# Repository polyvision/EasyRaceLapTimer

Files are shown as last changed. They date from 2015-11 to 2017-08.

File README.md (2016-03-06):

EasyRaceLapTimer

# EasyRaceLapTimer

EasyRaceLapTimer is a complete open source IR lap time tracker all-in-one solution for FPV racing quads.



What you get with EasyRaceLaptimer:

**Features:**

* host system for tracking the laps
* IR transponders (code & schematic files for building them) with a transmitting range of 2 to 4 meters
* 63 available transponder IDs when using the project transponders
* changing the ID via a push button on the transponder, no additional programming required (started with version 0.3.1 of the transponders)
* update transponders with new code (Arduino hardware needed)
* setup guide for building your Raspberry PI host station
* the host station is also a WiFi access point to change configs etc on the fly
* monitoring mode, you can watch the stats with your mobile phones
* add your own team logo to the monitoring mode
* detailed stats about pilots and races
* sound effects for various events in a race
* TCP/IP and serial connections support for receiving lap times and commands from other time tracking systems
* export race events to PDF
* standard practice/ time trial mode
* competition mode for racing events with time penalties (satellites needed)
* automatic restarting of a race session after a specified idle time
* and much more comming soon

**Important notices**

EasyRaceLapTimer works basicly with any IR transponder, as long as you provide code for interpreting the IR pulses. Just have a look at the *ir_daemon* tool.

Be sure to use the full size of your SD card on the Raspberry PI

    sudo raspi-config

# Important information

The documentation for the project can be found in the [/docs](https://github.com/polyvision/EasyRaceLapTimer/tree/master/docs) directory.
There's also a huge [RCGroups](http://www.rcgroups.com/forums/showthread.php?t=2538917) thread with lots of answered questions, images etc.

# Version 0.5.x

You can download a SD card image for the PI of EasyRaceLapTimer on the following pages:

http://www.airbirds.de
http://www.easyracelaptimer.com

There's also an introduction video to the system.

# file structure

**/docs**
  documentation of nearly every part of the package

**/web**

the rails application

**/Arduino**

all arduino sketches

**/ir_daemon**

the cpp daemon for receiving the IR pulses

**/datasheets**

schematic files and more for transponders etc.

# Installation

fetch the source via git with the following command

    git clone git@github.com:polyvision/EasyRaceLapTimer.git

more details of each indivial package can be found in the *docs* folder

# Contributors
 * [Peter Provost](https://github.com/PProvost)
 * [Peisel](https://github.com/peisel)
 * [p3root](https://github.com/p3root)
 * [Sven Michel](https://github.com/svenmichel)

# license

The complete project uses the [GPL V3 license](http://www.gnu.org/licenses/gpl-3.0.de.html)

**development and sponsoring by [AirBirds](http://www.airbirds.de)**

Logo Title Text 1

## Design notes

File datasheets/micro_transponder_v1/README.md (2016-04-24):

This is a transponder intended for indoor microdrones. It's not that bright, 
which is fine when flying only a few feet from the receiver. It's also very 
small, which is good when every milligram counts.

It can still be programmed using alligator clips on the sides. The lettering 
on the back will show you which pad goes where (PB0, PB1, etc.). See the 
ATtiny85 datasheet for how they connect to the physical pins and their 
extended features.

Solder the +5V and GND pads to the power. If necessary, a +3.7V input (such as 
from a 1S lipo cell) should be enough.

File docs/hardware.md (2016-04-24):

EasyRaceLapTimer

# Hardware

## IR Transponder

    1x Infrared LED 950nm (Example: LD 274-3 or TSUS5202)
    1x Resistor 33 Ohm
    1x Resistor 330 Ohm
    1x Transistor NPN TO-92 45V 0,1A 0,5W (Example: 2N2222)
    1x ATTINY 85-20 PU, DIP-8
    1x IC socket for the ATTINY

You will need a solder pad for each transponder, on which you will solder everything on to.

**important notice**
Transponder version 0.2 & 0.3.1 are both compatible with ERLT. You can use both at the same time with ERLT. The only difference between 0.2 & 0.3.1 is the way you change the ID of the transonder.

## Transponder 0.3.1
Have a look at the [transponder datasheet](/datasheets/easy_race_lap_timer_transponder_attiny85_rev3_schematic.png) to see how all these parts are getting soldered.

## Transponder 0.2
Have a look at the [transponder datasheet](/datasheets/easy_race_lap_timer_transponder_attiny85_schematic.png) to see how all these parts are getting soldered.

## Programmer

You will need a programmer for the ATTINY85 if you want to upload the software on your own. Either use an Arduino as an ISP to accomplish this or get [this programmer](https://www.sparkfun.com/products/11801).

If you choose the Arduino ISP solution, here's an example [how to accomplish this](http://highlowtech.org/?p=1695).

## Host Station

    3x TSOP 31238 38kHz
    1x Raspberry Pi 2 (Raspberry Pi 1 is not officially supported)
    long wires to connect the TSOP IR sensors to the Raspberry GPIO ports
    1x USB WiFi stick (Example: Edimax EW-7811Un)
    5V micro USB power supply for the Raspberry Pi, eg: a powerbank

    optional, a buzzer: CPM 121, but any other buzzer which can stand 5V will make it too.

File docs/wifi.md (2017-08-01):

EasyRaceLapTimer

## WIFI AccessPoint

    SSID: EasyRaceLapTimer
    Password: 0123456789

## Host-IP

Use the following URL to connect with your mobile phone or whatever device you are using

     http://192.168.42.1

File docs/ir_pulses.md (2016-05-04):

EasyRaceLapTimer

# EasyRaceLapTimer - IR Pulses

9 bits are getting used for sending the transponder id (token). There's one thing to know in our approach. IR space pulses are also bits!
With 9 bits, we have 6 data bits, so 63 transponder IDs in total.

## the format

the length of a ZERO and ONE pulse can be found for example in

    Arduino/TransmitterAttiny85v0.2

*remember that each second pulse is actual a space for the ir receiver*

    1 PULSE | 2 PULSE | 3 PULSE | 4 PULSE | 5 PULSE | 6 PULSE | 7 PULSE | 8 PULSE | 9 PULSE

**1 PULSE | 2 PULSE**

  both must be set zero, it's our header

**3 PULSE | 4 PULSE | 5 PULSE | 6 PULSE | 7 PULSE | 8 PULSE**

  the actual data bits for representing our integer val or better said the id of the transponder

**9 PULSE**

  checksum bit. Set it to 1 if the number of ONES in the data bits is uneven

## example

    id 14: ZERO | ZERO | ZERO | ZERO | ONE | ONE | ONE | ZERO | ZERO
    id  3: ZERO | ZERO | ZERO | ZERO| ZERO | ZERO | ONE | ONE | ONE

if you log the output of your IR receiver you would get something like this for the above examples

    id 14: PULSE 300 | SPACE 300 | PULSE 300 | SPACE 300 | PULSE 600 | SPACE 600 | PULSE 600 | SPACE 300 | PULSE 300
    id  3: PULSE 300 | SPACE 300 | PULSE 300 | SPACE 300 | PULSE 300 | SPACE 300 | PULSE 600 | SPACE 600 | PULSE 600

please keep in mind that the pulse length differs a lot when using IR receivers, so they won't be 100% accurate

## some statistics

The longest time an ID (63) needs to be transmitted is 2x 250&#181;s + 7 * 650&#181;s = 5050&#181;s = 5.05ms

Assuming your quad top speed is 120km/h, that's 33.33 m/s  =  3.33 cm/ms. So the distance needed to transmit the ID is 15cm.

Distance needed with a speed of 90km/h = 25 m/s = 2,5 cm/ms -> 13.75 cm distance

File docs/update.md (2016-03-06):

EasyRaceLapTimer

Instructions for updating to the next stable version. After updating the system, you need to restart the Raspberry PI.

# updating to 0.5
    cd ~/EasyRaceLapTimer
    git pull origin master

    cd ~/EasyRaceLapTimer/web
    bundle
    RAILS_ENV=production rake db:migrate
    RAILS_ENV=production rake assets:precompile
    
# updating from v0.3 to v0.4

    sudo apt-get install redis-server
    cd ~/EasyRaceLapTimer
    git pull origin master

    cd ~/EasyRaceLapTimer/ir_daemon
    qmake ir_daemon.pro
    make
    sudo ./ir_daemon --use_standard_gpio_sensor_pins (call this cmd after the update, this sets the standard pin layout for the sensors etc)

    cd ~/EasyRaceLapTimer/web
    bundle
    RAILS_ENV=production rake db:migrate
    RAILS_ENV=production rake assets:precompile

# updating to v0.3

    cd ~/EasyRaceLapTimer
    git pull origin master

    cd ~/EasyRaceLapTimer/ir_daemon
    sudo apt-get install libudev-dev
    qmake ir_daemon.pro
    make

    cd ~/EasyRaceLapTimer/web
    bundle
    RAILS_ENV=production rake db:migrate
    RAILS_ENV=production rake assets:precompile

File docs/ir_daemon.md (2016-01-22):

EasyRaceLapTimer

# EasyRaceLapTimer IR_DAEMON

The ir_daemon is a C++ daemon running in the background of your Raspberry PI. It's responsible for decoding IR data, receiving and sending commands from and to various sources etc.

## requirements

    sudo apt-get install  qt5-default libcurl4-openssl-dev libudev-dev

## compilation

    cd ir_daemon
    qmake ir_daemon.pro
    make
    sudo ./ir_daemon --use_standard_gpio_sensor_pins
    sudo ./ir_daemon [for starting]

## command line options

show some debug output

    --debug

listing available serial ports

    --list_serial_ports

set serial port

        --set_com_port_index INDEX

set buzzer pin

        --set_buzzer_pin PIN

use standard pin layout

        --use_standard_gpio_sensor_pins

use pin layout for displayotron 3k HATs

        --use_dot3k_hat_pin_setup

enable satellite mode

        --enable_satellite_mode

disable satellite mode

        --disable_satellite_mode

set web host URL, used for the satellite to set the right IP of the main station

        --set_web_host http://<IP>/

        default:

        --set_web_host http://localhost/

## data sources

   The ir_daemon can read data from TCP/IP sockets, serial connections and of course from the GPIO interface of the Raspberry PI.

## TCP Connection

The ir_daemon is listening on port 3006 for incomming connections. All commands need
a \n behind the #.

## commands

The following commands are available for serial and TCP/IP connections

*starting a new race*

    START_NEW_RACE#

*resetting*    

    RESET#

*tracking a new lap time*

    LAP_TIME <TOKEN/ID> <MILLISECONDS>#

* getting the last scanned token by the ir_daemon *

    LAST_SCANNED_TOKEN#

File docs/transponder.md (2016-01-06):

EasyRaceLapTimer

# Transponder setup

# Requirements

You will need the Arduino software and an ISP programmer (Arduino Nano, UNO, [Tiny AVR programmer](https://www.sparkfun.com/products/11801) ...)

Now add this url to the additional boards  in your Arduino IDE in the settings menu:

    https://raw.githubusercontent.com/damellis/attiny/ide-1.6.x-boards-manager/package_damellis_attiny_index.json

# Step 1

  Set the settings of your Arduino software like in this screenshot

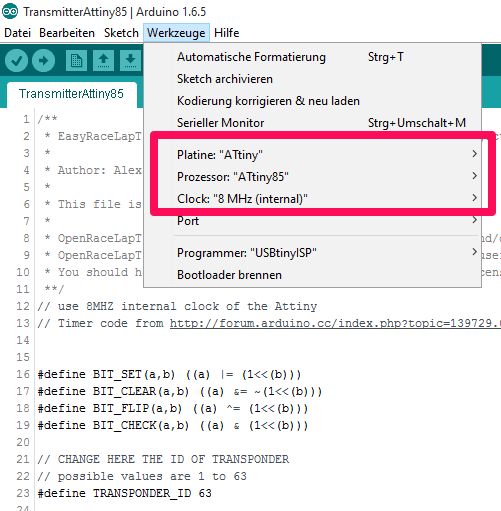
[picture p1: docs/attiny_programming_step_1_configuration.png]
  

# Step 2

  burn the bootloader

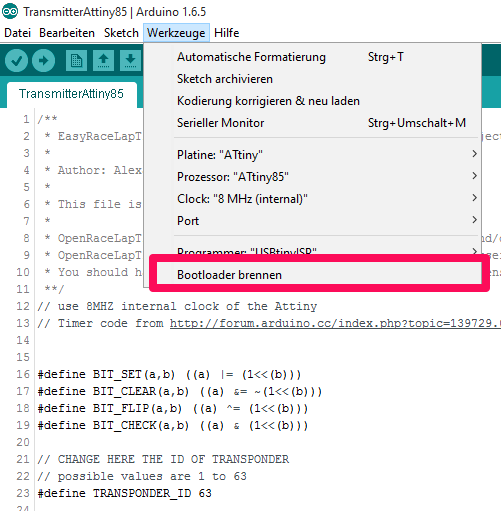
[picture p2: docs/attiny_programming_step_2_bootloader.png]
  

# Step 3

  change the ID of your transponder

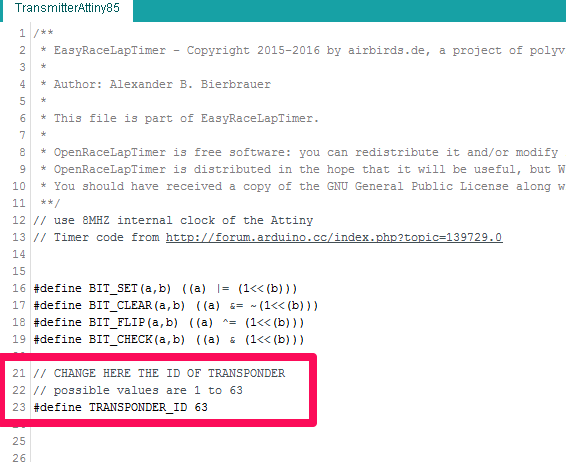
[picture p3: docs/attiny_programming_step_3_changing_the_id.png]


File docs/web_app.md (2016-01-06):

EasyRaceLapTimer

# EasyRaceLapTimer web application

this setup is based on Raspian JESSIE

## install requirements

switch to the **web** folder in your EasyRaceLapTimer folder

    sudo apt-get install ruby2.1-dev libssl-dev apache2 apache2-threaded-dev libapr1-dev redis-server libaprutil1-dev  imagemagick wkhtmltopdf redis-server
    sudo gem install bundler
    bundle config build.nokogiri --use-system-libraries
    sudo  gem install nokogiri -v "1.6.6.2"
    bundle
    sudo gem install passenger
    sudo passenger-install-apache2-module
    RAILS_ENV=production rake db:create
    RAILS_ENV=production rake db:migrate
    RAILS_ENV=production rake db:seed
    RAILS_ENV=production rake assets:precompile

## Apache setup

copy this code

    LoadModule passenger_module /var/lib/gems/2.1.0/gems/passenger-5.0.21/buildout/apache2/mod_passenger.so
    <IfModule mod_passenger.c>
      PassengerRoot /var/lib/gems/2.1.0/gems/passenger-5.0.21
      PassengerDefaultRuby /usr/bin/ruby2.1
    </IfModule>

and add it to the apache2 config via

    sudo nano /etc/apache2/apache2.conf

place the code near the following lines in the file

    # Include module configuration:
    IncludeOptional mods-enabled/*.load
    IncludeOptional mods-enabled/*.conf

## Rails Webapp setup

    rake db:create
    rake db:migrate
    rake db:seed

default credentials are:

    user: admin@easyracelaptimer.com
    password: defaultpw

## Rails Webapp development
for running rails in dev mode, you need to run these two commands in seperate processes (e.g. terminal windows). The app uses sqlite for it's database

    rails s

starting with v0.4, REACT gets used for various parts

    cd web
    npm install  (installing node modules)
    webpack (compiles the JS to app/assets/javascripts/main.js)

## API

be sure to change **localhost:3000** to the correct ip of the host station

**tracking a lap**

    POST http://localhost:3000/api/v1/lap_track

or

    GET http://localhost:3000/api/v1/lap_track/create

**starting a new race**

    GET http://localhost:3000/api/v1/race_session/new

**getting data of the current race session**

    GET http://localhost:3000/api/v1/monitor

needed params
 * transponder_token
 * lap_time_in_ms

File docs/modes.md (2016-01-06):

EasyRaceLapTimer

# EasyRaceLapTimer modes in detail

## standard mode aka practice / time trial mode

The most used mode. Fly your laps, the system tracks your time. You can check later on who was the fastest in the practice / event etc.

## competition mode

The mode used for racing events. The system sums up the time for each lap of a pilot. The one with the fastest summary time is the winner. If used with satellites, you can define time penalties if a satellite doesn't get passed.

In competition mode, you must set manually the pilots who are attending the race. You can define new transponder tokens especially for this mode or simple keep the old ones.

If you enable the hot seat feature in the competition mode, you don't need to add pilots. If a pilot passes the sensor, he will get added automaticly to the current race.

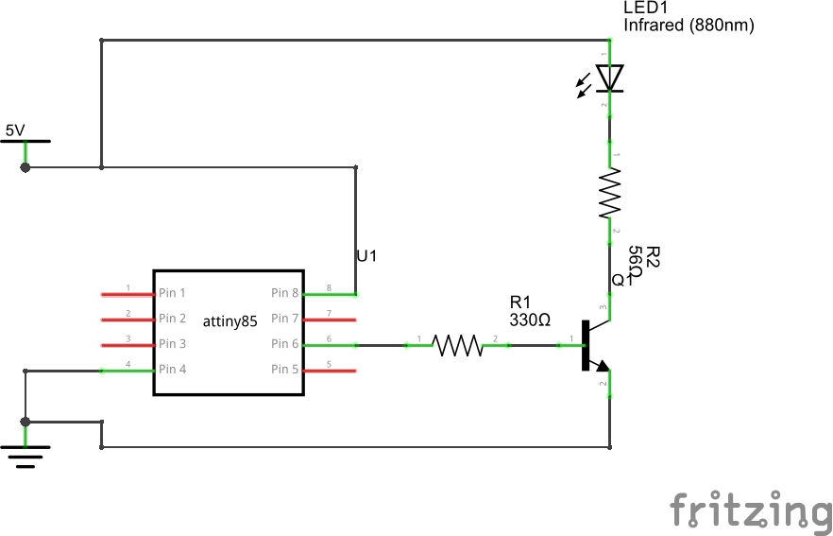
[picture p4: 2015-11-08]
datasheets/easy_race_lap_timer_transponder_attiny85_schematic.png

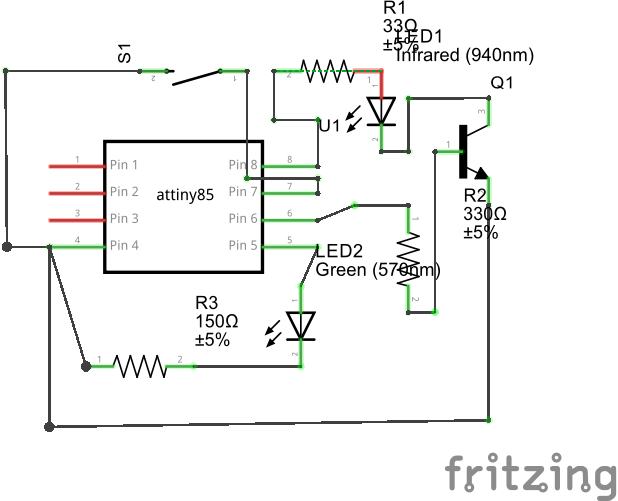
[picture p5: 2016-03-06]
datasheets/easy_race_lap_timer_transponder_attiny85_rev3_schematic.png

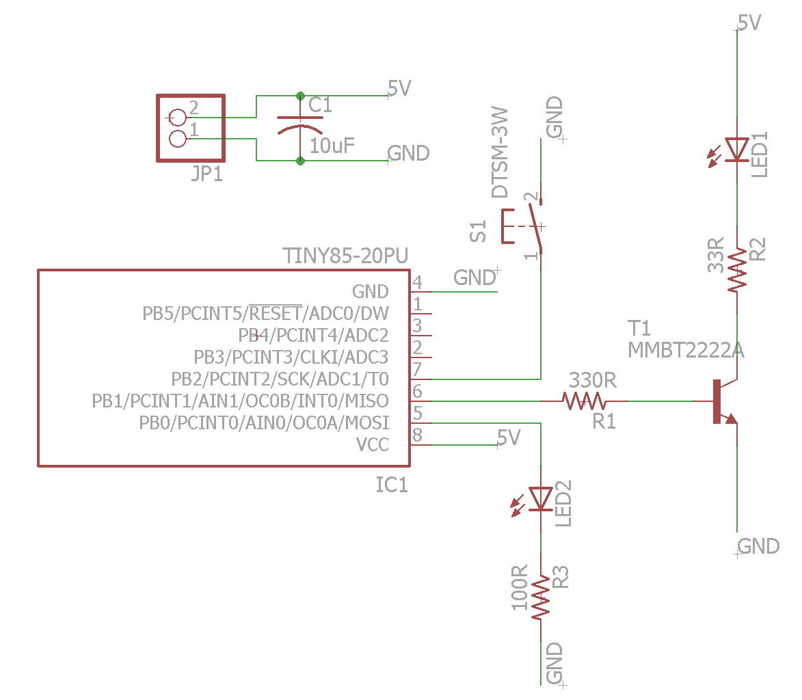
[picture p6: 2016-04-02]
datasheets/SMD Transponder/SMD R1.4 Schematic.PNG

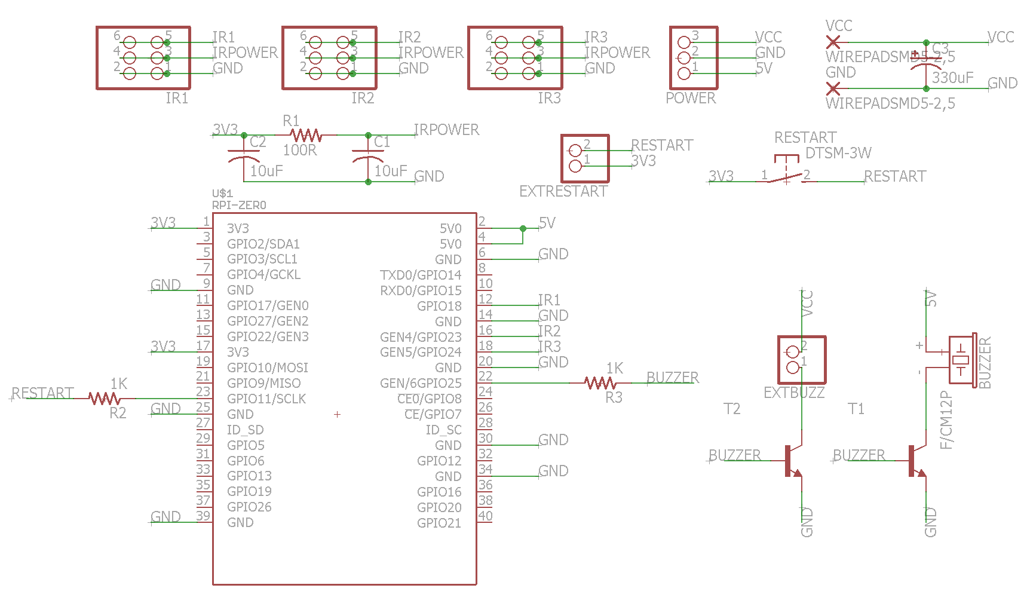
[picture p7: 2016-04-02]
datasheets/Raspberry Pi Hat Base Station/BaseStation R1.1 Schematic.png

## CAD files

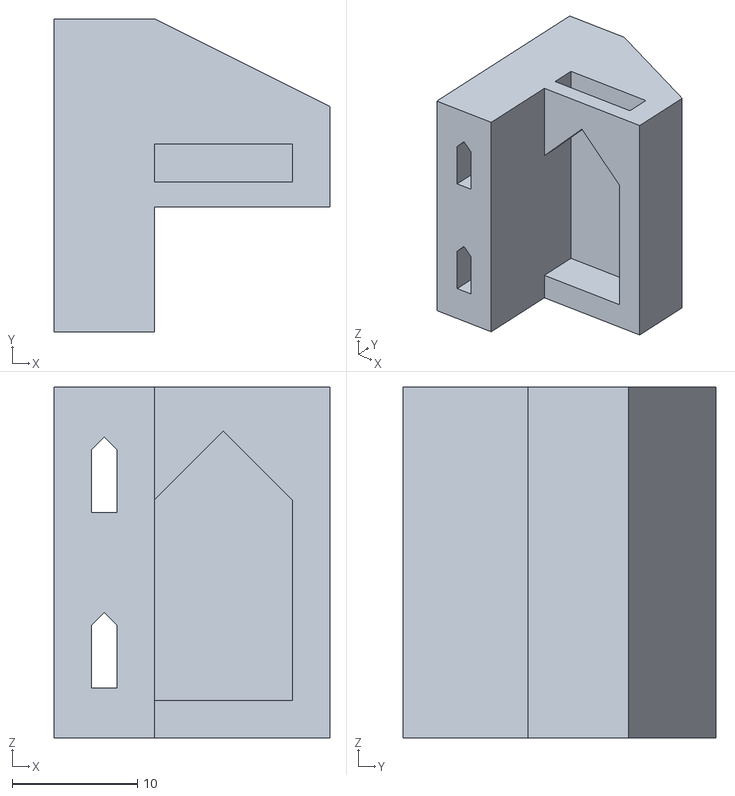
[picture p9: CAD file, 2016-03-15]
3d_print_files/ERLT Sensor Right - TSOP31238.stl
22.0 x 25.0 x 28.0

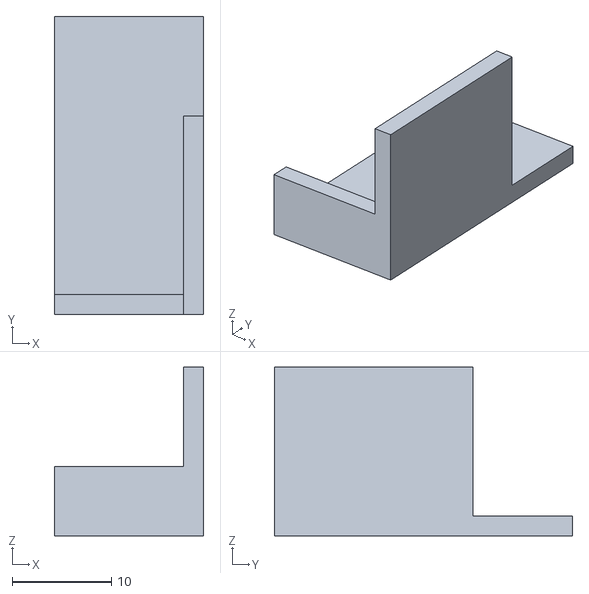
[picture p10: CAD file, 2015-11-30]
3d_print_files/sensor_case_left.stl
15.0 x 30.0 x 17.0

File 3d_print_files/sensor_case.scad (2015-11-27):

cube([15,30,2]);
translate([0,0,2]){
    cube([15,2,5]);
}

translate([13,0,2]){
    cube([2,20,15]);
}

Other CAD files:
3d_print_files/ERLT Sensor Left - TSOP31238.stl
3d_print_files/sensor_case.stl
3d_print_files/ERLT Sensor Left - TSOP31238.skp
3d_print_files/ERLT Sensor Right - TSOP31238.skp

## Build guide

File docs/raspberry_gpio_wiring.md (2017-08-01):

EasyRaceLapTimer

# EasyRaceLapTimer Raspberry2 PI GPIO wiring

The wiring should be the same of Raspberry 1 hardware. If not, feel free to update the docs.

# wiring
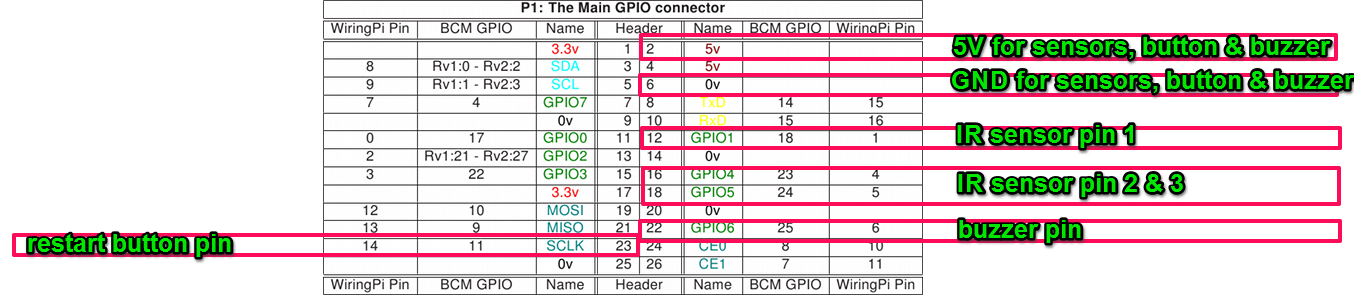
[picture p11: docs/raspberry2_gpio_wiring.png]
"GPIO wiring"


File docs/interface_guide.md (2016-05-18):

EasyRaceLapTimer

# Website pages and functions

This guide will walk you through the pages and functions of the EasyRaceLapTimer website interface.

When you go to the web interface (usually through http://192.168.42.1), you'll see this screen:

main

## Login

You can login by clicking the Login button on top.
Default admin login info is:

Email: admin@easyracelaptimer.com 
Password: defaultpw

After you logged in as admin, you'll see this screen:

afterlogin

Let's walk through the different pages.

## Race Director

On the Race Director page, you have control over the race in progress. You can start/stop races, check the latest detected Transponder ID, fastest laps, number of laps per pilot, etc.

## Configuration

### System

The System page allows you to:

* start Standard Race Tracking
* start a Competition Race (more advanced options)
* go to Pilots and Sound Configuration
* set some configuration values
* upload your own logo 
* shutdown the Raspberry Pi

### Users

The Users page allows you to create, edit and remove user profiles. You can also assign roles to users (admin/race director).

users

### Pilots

On the Pilots page allows you to add, remove and edit pilots info. 

pilots

* To add a pilot, fill in his/her Name, Transponder Token, Quad name and press Create.
* To remove a pilot, click the Delete button behind the pilots info in the list.
* To edit a pilots info, click the Edit button behind the pilots info in the list.
* You can remove the Transponder Token from the pilot by clicking the Remove Token button.

There is also the option to add an avatar to each pilot. This can be done by clicking the Edit button after adding the pilot to the list.

### Soundeffects

On the Pilots page allows you to adjust the audio Volume by pressing the buttons. You can also test the audio by pressing the Play Test Sound button.

soundeffects

You can also upload your own Race Event Soundeffects by clicking the Upload Wav button after every audio event listed.

## Monitor

The Monitor page allows everyone (pilots/audience) to follow the timing. It shows fastest laptime, last laptime, number of laps, average laptime per pilot.

## History

On the History page, you have an overview of all sessions. Each session shows some brief info like the name, mode, number of pilots, number of laps, fastest lap, fastest pilot and the average laptime of the session.

Behind each session row, you have the option to delete the session from history or export the results as a PDF-document.

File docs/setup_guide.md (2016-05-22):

EasyRaceLapTimer

# Complete Setup Guide

This guide will walk you through manually setting up the software on your Raspberry Pi. You will
need to have your Pi connected to the internet to perform these steps.

As an alternative, you can use the provided Raspbian disk image file if you have the exact same
hardware as described in the hardware setup doc and just want to get started right away. But if you want
to know how to build the software up from scratch, this guide is for you!

## Preparing your Raspberry Pi

Before you begin, you should download and install a Raspian Jessie image onto an 8GB (or more) micro SD card.
For more information about setting up your Pi, see https://www.raspberrypi.org/help/quick-start-guide/.

The next thing is to ensure that you are using all of your SD card. Execute the following command:

    sudo raspi-config

and choose "Expand Filesystem".

If you used NOOBS to install Raspbian, you can probably skip this step, but if you're unsure, try it anyway
and it will tell you if there is nothing to do.

While you are in raspi-config, you might also want to change whether the Pi boots to a desktop (GUI) or to
the command line. Since the system runs "headless", not running the full GUI can free up resources. If you're
unsure, leave it set to the default.

## Get the Code

On the Pi, execute the following commands to pull the source from this GitHub repository:

    cd ~
    git clone https://github.com/polyvision/EasyRaceLapTimer.git

## Build the IR Daemon

The IR Daemon listens for the signals coming from the IR detectors and sends them to the Rails app via
a web API.

To build it, perform the following steps:

    cd ~/EasyRaceLapTimer/ir_daemon
    sudo apt-get install  qt5-default libcurl4-openssl-dev libudev-dev wiringpi
    qmake ir_daemon.pro
    make
    sudo ./ir_daemon --use_standard_gpio_sensor_pins

## Build the Rails App

This is the main system app, and it provides the web UI & API.

To build it, perform the following steps (note: some of these steps will take a while to run, so be patient):

    cd ~/EasyRaceLapTimer/web/
    sudo apt-get update
    sudo apt-get install ruby2.1-dev libssl-dev apache2 apache2-threaded-dev libapr1-dev redis-server libaprutil1-dev imagemagick libsqlite3-dev bridge-utils wkhtmltopdf hostapd dnsmasq
    sudo gem install bundler
    bundle config build.nokogiri --use-system-libraries
    sudo  gem install nokogiri -v "1.6.6.2"
    bundle
    RAILS_ENV=production rake db:create db:migrate db:seed assets:precompile
    sudo gem install passenger
    sudo passenger-install-apache2-module

## Configure Apache Webserver

First you need to setup the new site in Apache:

    cd ~/EasyRaceLapTimer
    sudo cp config_files/000-default.conf /etc/apache2/sites-available/000-default.conf

Then, open /etc/apache2/apache2.conf using this command:

    sudo nano /etc/apache2/apache2.conf

In that file, find the following lines:

    # Include module configuration:
    IncludeOptional mods-enabled/*.load
    IncludeOptional mods-enabled/*.conf

and paste the following just before them

    LoadModule passenger_module /var/lib/gems/2.1.0/gems/passenger-5.0.21/buildout/apache2/mod_passenger.so
    <IfModule mod_passenger.c>
      PassengerRoot /var/lib/gems/2.1.0/gems/passenger-5.0.21
      PassengerDefaultRuby /usr/bin/ruby2.1
    </IfModule>

## Configure Linux Networking

The easiest way to setup the network is to use the provided interfaces file:

    sudo cp config_files/network_interfaces /etc/network/interfaces

But if you know linux networking, you might want to just compare the existing file with
the provided one and setup the network accordingly.

## Configure the Wireless Hotspot

If you are using the recommended EDIMAX WiFi adapter, you should skip to the section "Configuring
the EDIMAX WiFi Adapter".

If you are using another WiFi interface with your Pi, you should look at the following articles
to learn how to configure your interface for AP mode.

* http://jacobsalmela.com/raspberry-pi-and-routing-turning-a-pi-into-a-router/
* http://elinux.org/RPI-Wireless-Hotspot

You will then want to adapt the instructions below for your adapter.

### Configuring the EDIMAX WiFi Adapter

Source: http://www.daveconroy.com/turn-your-raspberry-pi-into-a-wifi-hotspot-with-edimax-nano-usb-ew-7811un-rtl8188cus-chipset/

First you need to get the updated driver for the RTL8188CUS chipset used in this interface:

    cd ~
    wget http://www.daveconroy.com/wp3/wp-content/uploads/2013/07/hostapd.zip
    unzip hostapd.zip
    sudo mv /usr/sbin/hostapd /usr/sbin/hostapd.bak
    sudo mv hostapd /usr/sbin/hostapd.edimax
    sudo ln -sf /usr/sbin/hostapd.edimax /usr/sbin/hostapd
    sudo chown root.root /usr/sbin/hostapd
    sudo chmod 755 /usr/sbin/hostapd
    cd ~/EasyRaceLapTimer
    sudo cp config_files/hostapd.conf /etc/hostapd/

Then reboot your Pi:

    sudo reboot

After rebooting, you can test your configuration using the following command:

    sudo hostapd -dd /etc/hostapd/hostapd.conf

If it runs as expected, add it to your system startup:

    sudo nano /etc/default/hostapd

Then uncomment and update the following line:

    DAEMON_CONF="/etc/hostapd/hostapd.conf"

Next you will configure the DNS & DHCP settings:

    sudo nano /etc/dnsmasq.conf

Find the line that begins with "#interface" and edit it as follows:

    interface=wlan0

In the same file, find the line that begins with "#dhcp-range" and edit it as follows:

    dhcp-range=192.168.42.2,192.168.42.100,255.255.255.0,12h    

Save and close the file.

## Check Permissions for wkhtmltopdf
Double check that the wkhtmltopdf is executable.  This ensures that "PDF Export" will work for race history.

    sudo chmod +x /home/pi/EasyRaceLapTimer/web/bin/wkhtmltopdf

## Check Permissions for sidekiq.sh
Double check that the sidekiq.sh script is executable

    sudo chmod +x /home/pi/EasyRaceLapTimer/web/start_sidekiq.sh

## Configure the IR Daemon and Sidekiq (sound events) to launch at startup

Edit the following file:

    sudo nano /etc/rc.local

Then add the following to the bottom of the file, just before "exit":

    (sleep 1; /home/pi/EasyRaceLapTimer/ir_daemon/ir_daemon > /var/log/ir_daemon.log 2>&1 &) || /bin/true
    (sleep 1; /home/pi/EasyRaceLapTimer/web/start_sidekiq.sh > /var/log/sidekiq.log 2>&1 &) || /bin/true

## Troubleshooting sound effects playback

Sidekiq is responsible for playback of audio for sound effects.  Depending on the version and source fo Ruby installed, Sidekiq may not launch at startup.  If this is the case, please try these steps.

Locate the path to the Sidekiq binary that is being used by Ruby:

    which sidekiq

Edit the following file:

    sudo nano ~/EasyRaceLapTimer/web/start_sidekiq.sh

Edit the following line by replacing sidekiq with the /full/path/to/sidekiq:

    RAILS_ENV=production sidekiq -c 1

## To login to the website:

Connect to your raspberry Pi (via Ethernet or the Pi's Wifi Access Point).

Default password for the Wifi AP is "raspberry".

Open the webpage, if you're connected via Wifi AP the address is http://192.168.42.1

Default credentials are:

    user: admin@easyracelaptimer.com
    password: defaultpw

*You are done!*

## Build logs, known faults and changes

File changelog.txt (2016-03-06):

version 0.5.1

* added autorestart of race sessions via idle time
* added transmitter code 0.3.1
* bug fixing

version 0.4b2

* webview monitor updates itself all 2 seconds
* sending monitor UDP broadcast after tracking a lack via port 3333
* renamed config values for better understanding
* improved GUI (not finished yet)
* added hot seat feature for competition mode

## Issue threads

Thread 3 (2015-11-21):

How to update the files in Raspberry PI

peisel, 2015-11-21:
It would be nice to have a description/manual how to simple update the solution on the Raspberry Pi to latest version.

PProvost, 2015-11-24:
I agree. For my most recent update, after pulling the new source, I had to reset the database using the rake commands in the setup guide. It is probably a good idea to explain that to people.

polyvision, 2015-11-29:
wrote update docs for 0.3 ;)

Closed 2015-11-29.

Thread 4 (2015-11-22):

Upload Soundfiles doesn't work

peisel, 2015-11-22:
Test with short .wav files, .mp3 files. Upload Button don't work.

polyvision, 2015-11-25:
fixed in upcomming v0.3

workaround for current version: go to sound page, reload the page, upload works. curious bug ;)

PProvost, 2015-12-17:
I'm in 0.4b2 and unable to upload sound files using the webpage. Nothing helpful in the apache2 error log file, and nothing at all in the easyracelaptimer.error.log file.

Closed 2015-11-25.

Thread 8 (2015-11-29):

Shutdown Button - No Function

peisel, 2015-11-29:
I did update via Update - not image. Shutdown Button didn't work after Popup OK. PI didn't shudown.

polyvision, 2015-11-29:
did u recompile the ir_daemon and made a restart of the complete system? the shutdown button should work

peisel, 2015-11-29:
Forget to restart the complete system - works

Closed 2015-11-29.

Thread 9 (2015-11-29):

Race Restart Button didn't work?!

peisel, 2015-11-29:
Update via commands - not the complete image.

I use a buzzer button - contact closed as long i pressed the button. Connected to 23(signal),25(gnd) pin. Did i miss something?
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

peisel, 2015-11-29:
Sorry i see it in my own picture ... wire wrong ... ;-)

peisel, 2015-11-29:
Sorry wiring is ok - issue exist

polyvision, 2015-11-29:
same here, try again after the restart ;)

peisel, 2015-11-29:
hmm ... how should it work ... i thought the current race will reset? or how should this button work?

polyvision, 2015-11-30:
if u push the button, a new race will get started

peisel, 2015-12-02:
Ich bekomme es nicht zum laufen ... der schalter verbindet pin 23 und gnd solange wie ich ihn gedrückt halte. Ich hatte einmal einen Eintrag "Race November 29, 2015 22:40	0	0	0.0s		0.0s" dies konnte ich aber nicht reproduzieren, Ich benutze img 0.2 mit dem manuellen update auf 0.3. Den Pin habe ich auch einmal mit Kabel auf gnd überbrückt aber dort das gleiche liegt also nicht am schalter.... ratlos

polyvision, 2015-12-03:
Ich habe jetzt gerade nicht das Layout vor mir. Aber Du hast + an den PIN-Eingang gelegt? Hm, aber warte bis ich nachher nachschauen kann, bevor ich jetzt Mist rede ;)

peisel, 2015-12-03:
Der Taster verbindet das Signal von PIN 23 (Rotes Kabel) mit GND Pin 25 (schwarzes Kabel) wenn er gedrückt wird, ich gehe davon aus etwas spinnt mit software oder pi nicht?

polyvision, 2015-12-04:
wie lange drückst du denn? also 1sek muss gedrückt werden damit etwas passiert, ist so in der software programmiert

peisel, 2015-12-05:
Keine Ahnung ... lange gedrückt, kurz gedrückt ... ich warte mal ab auf 0.4 ...

peisel, 2015-12-07:
when i connect pin 23 and 24 for a second it works ... is it right? Pin 23 reacts when its connected with a + signal?

Closed 2015-12-08.

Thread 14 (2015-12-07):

Setting an ID Without Reprogramming

frezik, 2015-12-07:
I noticed that the racer's unique ID has to be set in the code, with a maximum of 63 IDs.  It would be nice to be able to set this ID prior to a race without a full flash of the chip.

There are a few ways this could work. I2C, SPI, and Serial should all be available on the ATtiny85 chip. SPI in slave mode is a little wonky on Arduino (the library doesn't support slave mode directly). All three may have timing issues in the Arduino library due to the lack of a 16MHz crystal driving the chip.

A crude but effective means would be similar to how memory chips work. You set binary data with one bit per wire (across however many wires you have), and then "latch" a signal on another wire. When the chip sees the latch happen, it reads the values off the data wires to build the word.

With the IR LED taking up one wire, the ATtiny85 only gives us 3 data wires plus 1 latch. By doing this twice, you could send 6 bits, for 64 possible values.

A slightly easier way is to bump up to an ATtiny2313 and use a whole 8 wires. Comparing prices on Digi Key, this would add less than $1 to the cost for single orders, and an almost insignificant cost on bulk orders. The pin headers for this are also a tiny cost.

A further extension could be to use the Ardunio EEPROM library:

https://www.arduino.cc/en/Reference/EEPROM

Which would allow for maintaining the ID in between reboots.

polyvision, 2015-12-09:
There will be a new revision of the  transponders in the future. But at present, I'm focussing on the software.

polyvision, 2016-01-11:
Solved in a new rev of the transponders. Soon to be released.

Closed 2016-01-11.

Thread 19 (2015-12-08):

Update Documentation

peisel, 2015-12-08:
Please add commands for:
- clean up race history
- clean up racers
- Reset User Passwords
- edit "Admin" Account

polyvision, 2015-12-09:
What do you mean by "clean up racers" and "clean up race history"? One single button to delete them all?

peisel, 2015-12-09:
Not a ring to rule them all ... a button to delete all --- better would be a list functionality for delete ... like select all and unselect some ... to delete most of them ...

PProvost, 2015-12-17:
If you want to toss the entire database and start clean, you can do this:

    RAILS_ENV=production rake db:drop db:create db:migrate db:seed

The first command (drop) tosses the current database, then create, migrate and seed recreate it (similar to the steps in the setup guide).

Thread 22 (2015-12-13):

Monitor API - update speed

FieserKiller, 2015-12-13:
Hi,
I built an app which announces lap times, check it out: https://play.google.com/store/apps/details?id=de.my_fuzzy_logic.laptimeannouncer
Tested it on field today. We had 3 smartphones polling the interface every second. It worked, but I noticed a varying delay between a copter passing the sensor and his last_lap time changing in monitor.
It is usually ~5sec behind, sometimes a few seconds more or less.

polyvision, 2015-12-13:
Hi,

yes that's true at present. I'm firing and forget the "send lap time" requests at present, QT handles then the requests.
I'm planning to change this portion of the code, so that these requests will arrive faster in the rails app.

FieserKiller, 2015-12-13:
The perfect solution from the point of view of my app would be broadcasting monitor JSON over UDP to the network, whenever data changes.
This way we would cover 3 topics at the same time:
- Service discovery. Every device would find EasyLapTimers address easily by listening to UDP broadcasts on its WiFi interface
- No polling anymore, less load, less bandwith and power usage
- (Almost) real time monitoring data for everyone :)

polyvision, 2015-12-21:
It's implemented now, please test it ;)
Port is 33333.

There's now also a config value udp_broadcast_address which defaults to: 192.168.42.1

Maybe 127.0.0.1 is a better solution, dunno. First time, I'm doing something with UDP broadcasts.

polyvision, 2016-01-04:
The update speed in v0.4RC1 should be now even faster

FieserKiller, 2016-01-04:
Back from holidays - will test and implement into LaptimeAnnouncer App :) Thx

fape, 2016-11-06:
Do you know why udp broadcast was removed on 0.6 branch? see 222493ca67ae545545f2e10878e69f29285fb60d

Closed 2016-01-04.

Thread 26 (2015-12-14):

Auto update race panel

cmenard, 2015-12-14:
Currently one has to manually refresh the page to get updates during a race.  I'm wondering if we could use something like this https://github.com/chrismccord/sync to automatically update the page during a race session.

polyvision, 2015-12-15:
this gem looks interesting, will check it out

PProvost, 2015-12-17:
Honestly, I quick-n-dirty solution would be to use client-side auto refresh logic.

Something simple like:

    <meta http-equiv="refresh" content="10" />

Would do nicely.

polyvision, 2015-12-18:
fixed in upcomming v0.4b, made a quick solution. The gem also uses websockets. I would have the same problem like now with actioncable (also websockets).

Closed 2015-12-18.

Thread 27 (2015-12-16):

Building Transponder

sniperxnl, 2015-12-16:
I see no crystal on the Attiny85? Is that for a reason?

sniperxnl, 2015-12-16:
I have build the same on

1x Attiny85
1x 330Ohm
1x 56Ohm
1x NPN BC547
1x Vishay 950NM (i wait for the osram)

So i think i build a next one with crystal 8 MHZ and 2 x 10 pF on the gnd.

What do you think?

PProvost, 2015-12-17:
What do you think you need a crystal for? Are you thinking you need an external oscillator?

The transponder code expects the ATTiny to be running at 8MHz which the built-in oscillator is quite capable of handling. Trust me. I have a dozen of these working on my desk using nothing more than an ATTiny85, a 2n222A, two resistors and the IR LED.

polyvision, 2015-12-17:
Hey, there. You don't need a crystal. Like PProvost said, the internal oscillator works just fine in 8Mhz mode. Just burn the bootloader with 8Mhz (like described in the docs) and you're done.

Closed 2015-12-21.

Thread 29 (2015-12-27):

Add FPV Channel for Pilots

peisel, 2015-12-27:
Add in Configuration and Race Overview - Choose from 40 Ch

warrenjeffs, 2016-05-31:
please add this to the pilot page, will make it alot easier to know what channel they should be on.

mindmined, 2016-06-23:
sorry, has to fix my hardware and I am quite busy at the moment.
But I will add a nice setup menu, as soon as possible. But I bricked my arduino and have to solder a new one in.
Soon you see my new hardware with Lap Time in the OSD.

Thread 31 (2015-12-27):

Host/Slave System for Competition

peisel, 2015-12-27:
I would be nice to connect several pi/sensors stations together - so team pilots could have their own station and they could connect together for competition races. I think you did this allready?

pompushko, 2019-04-30:
Nice Feature  would be , if use start and finish slave stations. and couple of stations in the middle to see time between portals

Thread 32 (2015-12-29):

Updated docs to include steps to install and build dependency wiringPi

Nandox7, 2015-12-29:
The wiringPi library is missing from the installations steps.

polyvision, 2016-01-04:
Would be great if you update the docs!

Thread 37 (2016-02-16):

Feature Request: Multicolor LED output for gates based on last pilot through.

c3h5, 2016-02-16:
I typically fly in small groups all via FPV and basically we cannot keep track of each other.
So I had an idea to allow color assignment to pilot’s transponder IDs in the software and have a hardware output from the Raspberry Pi to set multi colored LED.
The purpose would be so that the Raspberry Pi could control the multicolored LED display attached to a gate so that the pilots flying could see who flew though a gate last.
Example my friends color is blue and I see the gate ahead is blue thus he beat me to it.
But then some laps later I see a gate ahead and it’s my color, thus I know I’ve lapped him.

Hope the above makes sense

I think this would be great in a multi gate setup
and also having the option of the gates auto clearing of color after a users predefined amount of time.

frezik, 2016-02-16:
I happen to have been working with RGB LEDs of late. An easy way to do this is with GPIO, which would give you the 3 primary RGB colors, plus the 3 secondaries by combining any two of the 3 primaries.

It's possible to get any arbitrary color using PWM on each of the RGB colors, but the Pi only has 1 PWM output. You can use an Arduino to take an i2c or serial signal that sets the color, and then use its own PWM outputs to the LEDs.

c3h5, 2016-02-17:
This would be fine as the number of people flying at the same time is typically small and we care more about a quick head to head battle than say a best time. And powering a Pi/LED display is no big deal when you have plenty of old 3s lipo nobody is using. :)

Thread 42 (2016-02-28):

Spoken Lap Times

kah00na, 2016-02-28:
When the Raspberry Pi 2 is connected to an external set of speakers, it would be good if each lap time was spoken out loud so racers would know if they were getting faster or slower.  Lap times can currently be reviewed in the pilot's history through the web GUI after the race is over, but you don't know how you are doing during the race itself unless you have someone watching the Monitor page and yelling out the times.

polyvision, 2016-05-02:
Problem at present is the text-to-speech caps of the PI. I've tested some packages but the output is really  bad.

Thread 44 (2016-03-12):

Reliability of IR Protocol Desgin for Partial Codes

frezik, 2016-03-12:
Looking over the existing IR protocol design:

https://github.com/polyvision/EasyRaceLapTimer/blob/master/docs/ir_pulses.md

I thought of a situation that doesn't seem to have a solution in the current system (though I may have missed something). The data stream starts with a 300us pulse and 300us space as a header. It then alternates between pulses and spaces, with a 1-bit sent as 600us and 0-bit as 300us.

Here's the issue: let's say the quadcopter flies in range of the sensor just as it sends the second bit after the header (which will be a space). The sensor will see this as a single long space after the last quadcopter left the sensor range. Let's say the next pulse and space (third and fourth bits after the header) both happen to be 0. This will be detected as the start of a new header, and bits will be parsed from there as if the code had just started--obviously not the correct situation!

Since the quadcopter's transponder will keep cycling the same code, the next header will be parsed as a pair of zeros in the middle of a code. The software doesn't have a chance to recover.

This can be corrected by dealing with a longer code. The current equation on the page suggests that in the worst-case of a quad travelling at 120km/s, the complete code would be transmitted over the course of 15cm of movement. I suggest designing for 3 or more sensors wired in parallel to allow a budget of at least 30cm. This would be a marginal additional cost with slightly more complicated wiring.

With that change, the header can be changed to a 1200us pulse/1200us space. This allows the sensor code to easily throw away the initial partial code, then pick up the next good code. Duplicates sent in a short time period need to be thrown out, but that's true, anyway.

I'd also recommend sensor designers wire multiple receivers for at least 60cm. That gives the system the best chance of correctly picking up the code.

c7devteam, 2016-03-13:
OK, I get the point. I made some thoughts about this in the past too.

The only solution I can up was, add a crystal (or use another IC) to the transponder for more correct pulses (timings) and do the parsing of the codes via interrupts in the ir_daemon.

Regarding your solution, don't know if this will fix the problem (neither do I know if my suggestion will fix it) but let's try yours.

polyvision, 2016-03-13:
OK, I get the point. I made some thoughts about this in the past too.

The only solution I can up was, add a crystal (or use another IC) to the transponder for more correct pulses (timings) and do the parsing of the codes via interrupts in the ir_daemon.

Regarding your solution, don't know if this will fix the problem (neither do I know if my suggestion will fix it) but let's try yours.

frezik, 2016-03-13:
I think it will be a combination of the two--longer header length, and an external crystal.

I've been playing with some transmitters on a custom PCB, and using LIRC to get the raw pulse/space data. With an attiny85 on its internal 8MHz clock, the data is all over the place.

I then pulled the attiny out of its socket and used jumpers from an Arduino (atmega328, 16MHz external crystal) to hit the right pins in the socket to drive the circuit. I used a sketch based on the sendRaw example from the Arduino-IRremote library, which you can see here:

http://pastebin.com/cM0NEcM4

Using the same circuit board, those numbers came out as clean as can be expected for IR pulses. I doubt the switch to the atmega matters.  It's the clock that's doing it.

As another experiment, I set the attiny85 for a 1 MHz internal clock. Those numbers came out almost as clean as the Arduino. The only problem was that it wasn't quite fast enough to switch at 300us. The data bits almost always came out at 600us.

The one thing is that from these tests, I would have expected this to be all but unusable. Seems like there's enough people using the system "in the wild" that somebody would have noticed that by now.

frezik, 2016-03-13:
After testing again, I think it's actually working fine with the 300us timing on the 1MHz clock. See:

https://github.com/frezik/EasyRaceLapTimer/blob/ir_daemon_v2/Arduino/TransmitterAttiny85v0.4/TransmitterAttiny85v0.4.ino

This also removes the delay at the end of the loop. I believe this is what may have been helping the previous system to recover. With a longer header length, it shouldn't be necessary. In practice, removing that delay is likely to shorten the effective distance needed for a clean read, since the transmitter can send more duplicate codes.

It also does an infinite loop with `while(1){...}`.  This is faster than waiting for `loop()` to be continuously called.

The docs were also cleaned up, with issue #43 cleaned up, and the protocol header redefined. The math at the end for the length of the transmission was also corrected for the new header. I figured it was worth keeping the previous doc around while transmitters are still out there, so I moved it into `ir_pulses_old.md`.

This branch also has some of my work for the v2 ir_daemon, which runs off LIRC.

ABLomas, 2016-09-15:
If you are changing protocol anyway (requires transponder reflashing, etc) - maybe add single-bit checksum too?
One bit checksum for 6 bits of data (for example, XOR'ed) - does not add much payload, but would filter random ID's appearing in list (this happens sometimes). Usually ID can be read several times when going trough gate, so ID with mistake is not big issue.

I'm not sure how this plays with new ir_daemon - maybe requires many changes?

slacker87, 2016-09-15:
Pass the id number through an xmodem crc and then tack the resulting checksum at the end of the signal. If on the rx side the checksum doesnt add up to the id sent, discard as its an invalid (1/2 received) signal. This should work regardless of timing.

shamshir1972, 2017-03-12:
frezik, how do i run ir daemon v2, i.ve already install lirc dan cpan

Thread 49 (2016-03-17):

UDP multicast of raw gate events

rccrashcraven, 2016-03-17:
Rather than clients polling for monitor data, and rather than getting all data, it might make sense to have a udp multicast of each raw event. This would cut down a lot is load on the Pi server. Rather than the full session plus data json structure, just send a simplied token, lap num, lap time structure.

frezik, 2016-03-17:
I like this idea in theory. However, multicast can be tricky to setup in practice. It may be particularly tricky on Android and iOS clients (not sure, really).

If load on the Pi due to polling is high, we may be better off finding a way to reduce or offload that.

rccrashcraven, 2016-03-17:
Ok. I haven't looked at ease of multicast listeners on any thing except windows.

How many tcp client sockets can the PI hold open?
Maybe clients request connection, are given a port, reconnect at that port, then they are send raw gate events.

I have to think the load on PI would be much lighter than the same clients banging away at xxx/api/v1/monitor and which sends about many times the data required on a per event quad/gate event.

NicoLoco, 2016-05-06:
I like the idea of the Pi multicasting the information.
I would be careful with UDP as there is no guarantee the packets will be received, and Wifi can be flaky, especially in an environment full of other 2.4GHz and 5.8GHz signals.

Maybe we could setup a system where the server multicasts the last 10 events periodically via UDP.
If a client realises he is missing some events (missing IDs), it can send a request to the server asking for all events starting from event number X. This request would be handled in TCP so we know the server will receive it, and the reply will be received too.

SSPW, 2016-05-06:
I agree UDP is fire and forgot with no guarantees.

I think the only thing that should be guaranteed in the ERLT system is the PI actually has all the data and one master connection (a laptop of other that is the race admin portal). Any other system hanging off the PI, like a text to speech client is secondary and should be prioritized that way.

I race with a group that has 30 guys turn out. Lets say 20 try to listen using a client that is polling the normal monitoring api. Its going to bog down the PI. Sure there should only be 5-6 connected. But they aren't going to start and stop their connections. Its a bad scheme.

Alternative is a TCP server that client registers with transponder ID or all data. Then client then only gets event data they registered for. Client is simple. Server is more complicated.

WIFI default ERLT PI2 based build sucks!!! We tried it for 5-6 full days sessions. Tested macs, pc, and IOS and android clients. Connection reliability was horrible. Connection often would restore without rebooting the PI. We have abandoned it. We run a wired connection to our main laptop for 4 weeks. Zero issues with cable. Zero issues with the PI. Never have to reset the PI.

We wont be returning to PI based WIFI. We are considering putting a WAP in the system. WAP wired both the PI and laptop. Other clients then could connect on reliable WAP based WIFI.

I don't think UDP to individual transponder clients or bulk update clients is a bad thing. The only time UDP message is missed is when there is no network! With wired connection that is basically NEVER! Single broadcast for all SECONDARY clients leaves the PI unloaded.

I have working code, ie 2 Python scripts that implement UDP broadcasts. One scripts sit on the PI and polls the ERLT SQLLite database (not the web based monitor api). If it sees a change in either the race session or the sees any new transponder gate events (since the previous DB query), it broadcasts a UDP message with ONLY the updates. There no extra data, ie unchanged info sent!

I also have a Python client that runs on IOS and other platforms, that receives the UDP messages.

Its bullet proof in wired testing. Its equally reliable with a reliable wifi network.

This scheme is much more efficient on both ends!

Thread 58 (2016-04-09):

Display Transponder ID in two sets of LED Flashes broken

vcazan, 2016-04-09:
Currently if I flash the latest version of 0.3.1 that is in the master, attiny gets stuck in setup function in this for loop:

```
for (int i = 0; i < transponder_id / 10; i++) { //Display MSB
```

polyvision, 2016-04-13:
I've merged a pull request regarding this bug. Please check it out.

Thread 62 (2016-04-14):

broken link

NicoLoco, 2016-04-14:
in the documentation, hardware.md points to a schematic for the transmitters version 0.3.1, but the link is broken
https://github.com/polyvision/EasyRaceLapTimer/blob/master/datasheets/easy_race_lap_timer_transponder_attiny85_rev3_schematic
error 404

TimJC513, 2016-04-15:
I submitted pull request #64 with the fix for this.

polyvision, 2016-05-06:
got merged, thanks!

Closed 2016-05-06.

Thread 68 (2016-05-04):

lack of satellite instruction

tb942, 2016-05-04:
our flying group has almost finished building the main lap timer, but i am wanting to know how to set up / how the satellites work?
i.e. what method is used for the connection to the base station, and how you put it into satellite mode

LudoVicious, 2016-05-17:
Looking at the code, I don't think Satelite mode is fully implemeted yet (it sends satelite tracked messages to it's own webhost adress). But please correct me if i'm wrong. I would really like to put my ERLT in sat mode too.

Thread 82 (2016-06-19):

Bug Crashing IR demon when using pocket edition connected to GPIO.

SnipeXR, 2016-06-19:
Initial investigation in version 0.6 the ir daemon crashes when getting bombarded with trigger events from pocket edition.
Current patch to keep ir daemon running is a bash script in a forever loop recovering the IR_Deamon App.
Crashes seem intermittent and are more likely to occur when the trigger condition happens.

polyvision, 2016-08-01:
Yeah, it crashes a lot at present with the pocket edition. Working on it!

polyvision, 2016-08-22:
Just some news. I'm working on a NodeJS version of the ir_daemon. It's much less code and easier for other people to contribute.

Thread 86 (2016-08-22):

Powering the transponder

tlayh, 2016-08-22:
Hi, I am currently trying to build the transponders for the EasyRaceLapTimer in version 0.2. My question now, is it possible to power the transponder with 6v instead of 5v? I was thinking about adding a small battery pack for powering the transponder. That way I could use it without soldering some wires to the quad. Best way for a battery pack I found are to use two cr2032 with a switch to power it on and off.

Greetings,
Thomas

frezik, 2016-08-22:
The attiny85 datasheet lists 5.5V as its max operating voltage. You might get lucky, but I wouldn't count on it.

You could get away with powering at 3V, but the LED will be dimmer since the current-limiting resistor is higher than it needs to be at that voltage.

Any reason you don't want to take power off the flight controller or something like that? The Naze32 (and similar FCs) almost always have a spare 5V output pin somewhere.

tlayh, 2016-08-22:
Thanks for your answer. Main reason for not using the FC for me would be to allow guest pilots to easily add the transponder. But I think it should work if I put two diodes in front, they should lose 1V and then I can use the 6V battery pack. I let you know if it works ;)

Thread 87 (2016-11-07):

IR not receiving...

sleepingshorty, 2016-11-07:
Hi.

Thank you for your great work. I hope we can get it working.

My problem is, that the IR-Deamon does not receive any ID. We double checked the wiring, changed the receivers, reinstalled everything, but it isn't responding to the ir signal. We also flashed the Attiny85 again and checked that it is sending by using a camera.
We proved that the IR-Receiver is working by printing out the gpio read 2.

It's running on a Raspberry PI 3.

Every tutorial is about the IR-Deamon, in our setup there is only the IR-Deamon2.

Is it standard to use vtx and we have to change it somewhere? We had not found any config to change

Thanks for any help in advance!

Kind regards,
Torsten

spuder, 2017-08-01:
Did you ever get this working?

https://www.facebook.com/groups/1015588161838713/

On the facebook group someone claimed that the 6.x version doesn't work with IR. You need to install the older 5.x version. (I can't verify this yet since I can't get it working either)

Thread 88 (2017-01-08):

Betaflight transponder code implementation

IB1387, 2017-01-08:
Hi guys,

are there any plans to implement the ir code into betaflight? I recently built a ERLT base station and the setup with my omnibus f3 fc (which has all the required hardware except the ir led on board) would make tracking really simple and the setup really clean. I prefer the ir-based systems to the vtx-based systems for easy of use, cost and configuration reasons. I'd like to assign an ir-code to every person that wants to track their times and not have to configure vtx channels that change quite often.
I would be very grateful if somebody could take a shot at this. @polyvision you proposed to take a look at this, if theres a timer left in betaflight some time ago. Could you take a look at this, if you're not too busy? I'd be glad to help testing it, if I can. Sorry if that's much to ask for.

-1387

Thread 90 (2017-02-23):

Integrate with racebox hardware

SnipeXR, 2017-02-23:
Add racebox vtx timing hardware USB serial connection to enable wireless or wired Ethernet To wireless routers to enable mobile phone management and increase connection reliability.

Eliminate long distance USB extenders and replace with raspberry pi to Ethernet bridge connectivity and rabble mobile apps that can communicate via ip protocols.

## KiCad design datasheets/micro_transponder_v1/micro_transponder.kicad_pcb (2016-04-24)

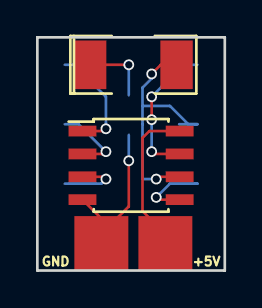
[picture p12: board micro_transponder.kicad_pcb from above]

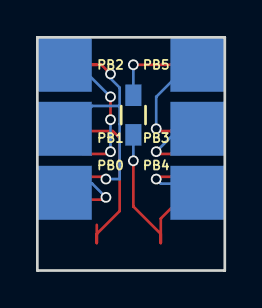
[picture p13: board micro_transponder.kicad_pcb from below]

Board: 2 copper layers, 10.4 x 13.0 mm, 9 parts (7 on the bottom side), 8 nets.

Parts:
D1: LED; SMD-2010_Pol
IC1: ATTINY85-S; SOIC-8_3.9x4.9mm_Pitch1.27mm
P1, P2, P3, P4, P5, P6: CONN_01X01; Measurement_Point_Square-SMD-Pad_Big
R1: 150 Ohm, 0.25W; R_0603_HandSoldering

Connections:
GND: IC1.4, R1.2
unnamed: D1.1, R1.1
unnamed: D1.2, IC1.6, P2.1
unnamed: IC1.1, P6.1
unnamed: IC1.2, P4.1
unnamed: IC1.3, P5.1
unnamed: IC1.5, P1.1
unnamed: IC1.7, P3.1

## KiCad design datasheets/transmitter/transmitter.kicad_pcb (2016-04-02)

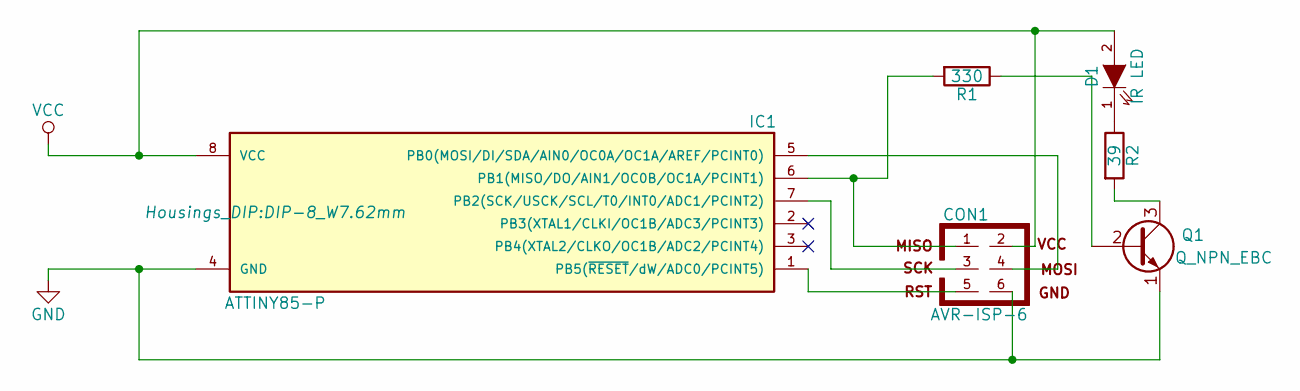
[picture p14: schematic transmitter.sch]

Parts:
CON1: AVR-ISP-6; Pin_Header_Straight_2x03
D1: IR LED; Pin_Header_Straight_1x02
IC1: ATTINY85-P; DIP-8_W7.62mm
Q1: Q_NPN_EBC; TO-92_Inline_Narrow_Oval
R1: 330; Resistor_Horizontal_RM7mm
R2: 39; Resistor_Horizontal_RM7mm

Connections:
GND: CON1.6, IC1.4 (GND), Q1.1 (E)
unnamed: CON1.1, IC1.6 (PB1(MISO/DO/AIN1/OC0B/OC1A/PCINT1)), R1.2
unnamed: CON1.3, IC1.7 (PB2(SCK/USCK/SCL/T0/INT0/ADC1/PCINT2))
unnamed: CON1.4, IC1.5 (PB0(MOSI/DI/SDA/AIN0/OC0A/OC1A/AREF/PCI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)
unnamed: CON1.5, IC1.1 (PB5(~RESET~/dW/ADC0/PCINT5))
unnamed: D1.1 (K), R2.1
unnamed: Q1.2 (B), R1.1
unnamed: Q1.3 (C), R2.2
VCC: CON1.2, D1.2 (A), IC1.8 (VCC)

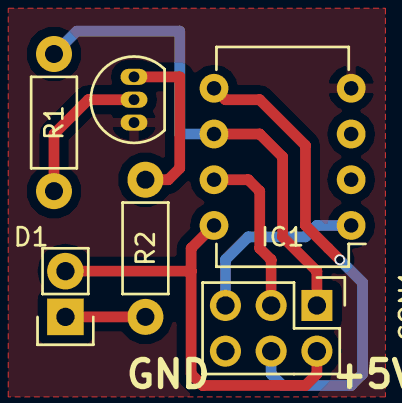
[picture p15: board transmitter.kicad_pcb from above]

Board: 2 copper layers, 6 parts (0 on the bottom side), 9 nets.

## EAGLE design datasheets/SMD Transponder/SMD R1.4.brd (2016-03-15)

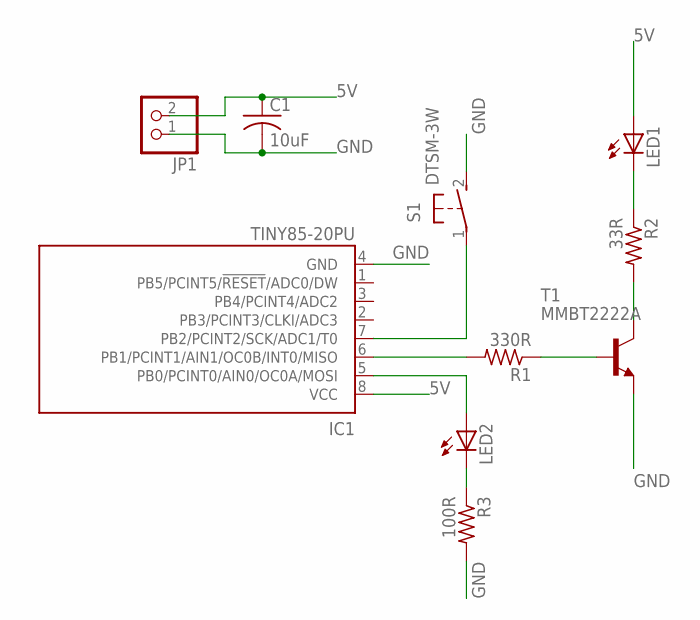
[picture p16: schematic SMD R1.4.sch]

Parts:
C1: 10uF; C1206K
IC1: TINY85-20PU; 8S2
JP1: PINHD-1X2; 1X02
LED1: LED5MM
LED2: LEDSML1206; SML1206
R1: 330R; R1206W
R2: 33R; R1206W
R3: 100R; R1206W
S1: DTSM-3W
T1: MMBT2222A; SOT23-BEC

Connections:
5V: C1.1, IC1.8 (VCC), JP1.2, LED1.A
GND: C1.2, IC1.4 (GND), JP1.1, R3.2, S1.2, T1.E
unnamed: IC1.5 (PB0/PCINT0/AIN0/OC0A/MOSI), LED2.A
unnamed: LED1.K (C), R2.1
unnamed: R2.2, T1.C
unnamed: R1.1, T1.B
unnamed: IC1.6 (PB1/PCINT1/AIN1/OC0B/INT0/MISO), R1.2
unnamed: LED2.C, R3.1
unnamed: IC1.7 (PB2/PCINT2/SCK/ADC1/T0), S1.1

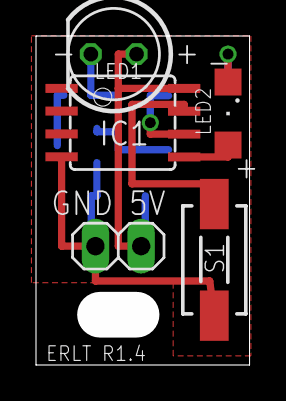
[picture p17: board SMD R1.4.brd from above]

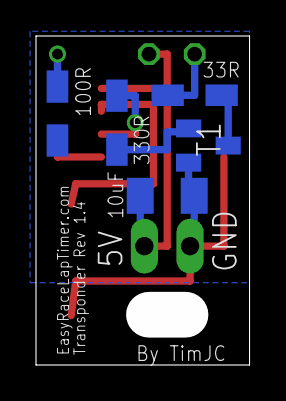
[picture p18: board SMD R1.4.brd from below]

Board: 2 copper layers, 11.9 x 18.3 mm, 10 parts (5 on the bottom side), 9 nets.

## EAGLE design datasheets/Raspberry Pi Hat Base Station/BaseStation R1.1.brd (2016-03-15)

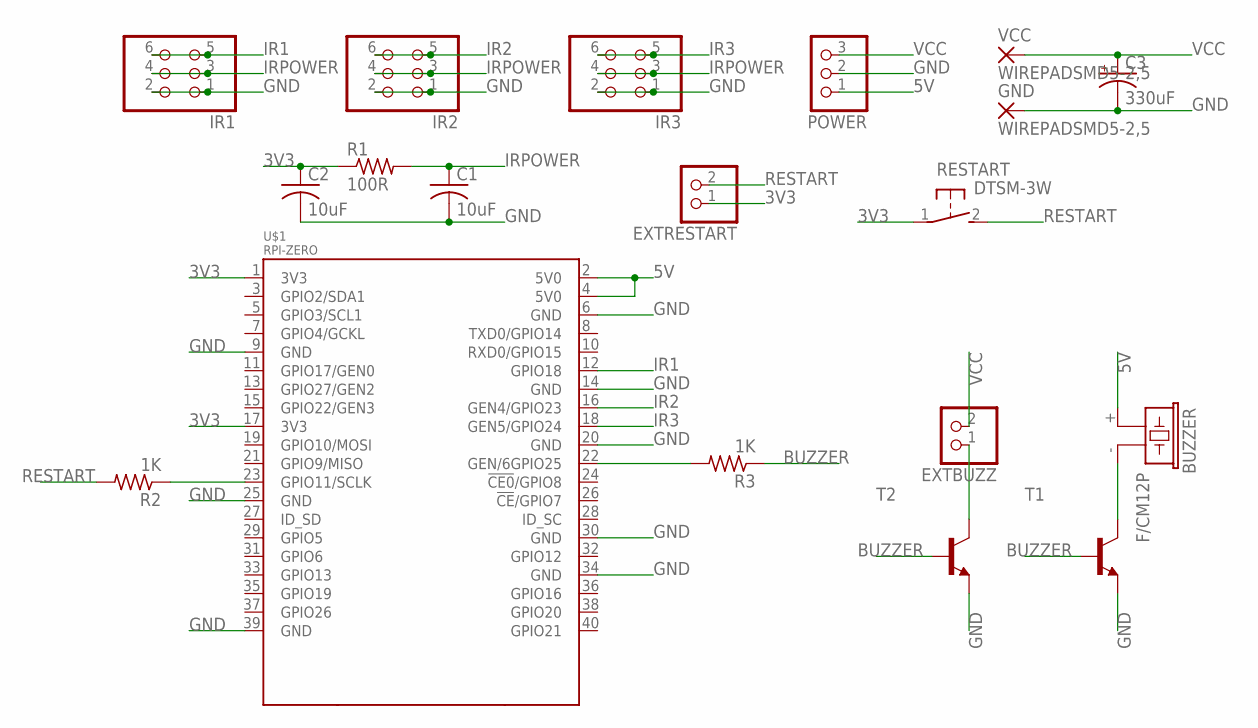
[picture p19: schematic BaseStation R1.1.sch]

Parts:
BUZZER: F/CM12P
C1, C2: 10uF; C1206K
C3: 330uF; E3,5-8
EXTBUZZ: PINHD-1X2; 1X02
EXTRESTART: PINHD-1X2; 1X02
GND: WIREPADSMD5-2,5; 5-2,5
IR1, IR2, IR3: PINHD-2X3; 2X03
POWER: PINHD-1X3; 1X03
R1: 100R; R1206W
R2, R3: 1K; R1206W
RESTART: DTSM-3W
T1, T2: MMBT2222ALT1-NPN-SOT23-BEC; SOT23-BEC
U$1: RPI-ZERO; RASPBERRYPI_BASTELSTUBE_V13_RASPI_BOARD_B+_FULL
VCC: WIREPADSMD5-2,5; 5-2,5

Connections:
3V3: C2.1, EXTRESTART.1, R1.1, RESTART.1, U$1.1 (3V3), U$1.17 (3V3)
5V: BUZZER.+ (1), POWER.1, U$1.2 (5V0), U$1.4 (5V0)
BUZZER: R3.1, T1.B, T2.B
GND: C1.2, C2.2, C3.-, GND.1, IR1.1, IR1.2, IR2.1, IR2.2, IR3.1, IR3.2, POWER.2, T1.E, T2.E, U$1.6 (GND), U$1.9 (GND), U$1.14 (GND), U$1.20 (GND), U$1.25 (GND), U$1.30 (GND), U$1.34 (GND), U$1.39 (GND)
IR1: IR1.5, IR1.6, U$1.12 (GPIO18)
IR2: IR2.5, IR2.6, U$1.16 (GEN4/GPIO23)
IR3: IR3.5, IR3.6, U$1.18 (GEN5/GPIO24)
IRPOWER: C1.1, IR1.3, IR1.4, IR2.3, IR2.4, IR3.3, IR3.4, R1.2
unnamed: R2.1, U$1.23 (GPIO11/SCLK)
unnamed: R3.2, U$1.22 (GEN/6GPIO25)
unnamed: BUZZER.- (2), T1.C
unnamed: EXTBUZZ.1, T2.C
RESTART: EXTRESTART.2, R2.2, RESTART.2
VCC: C3.+, EXTBUZZ.2, POWER.3, VCC.1

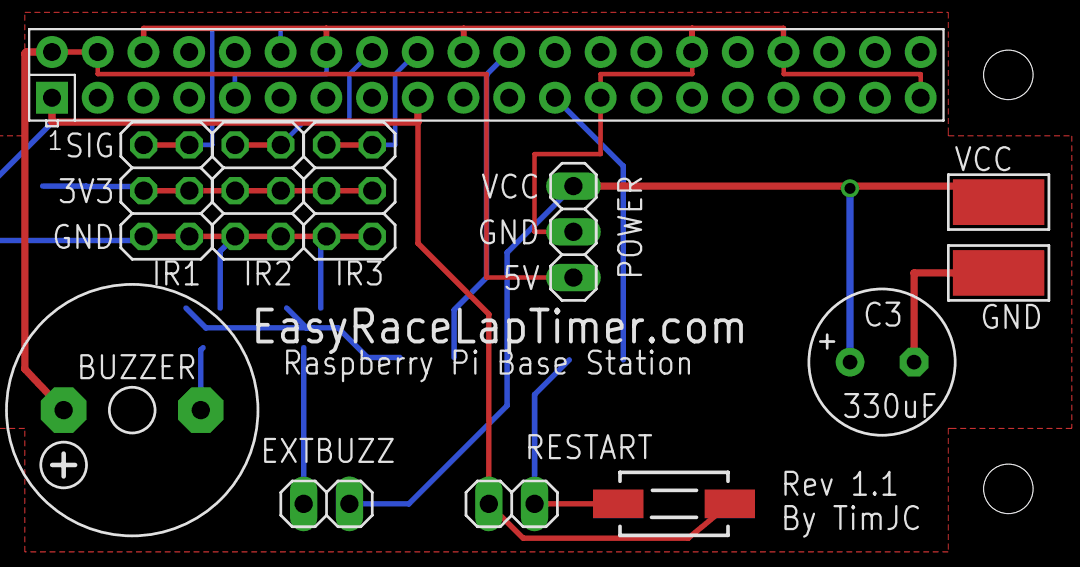
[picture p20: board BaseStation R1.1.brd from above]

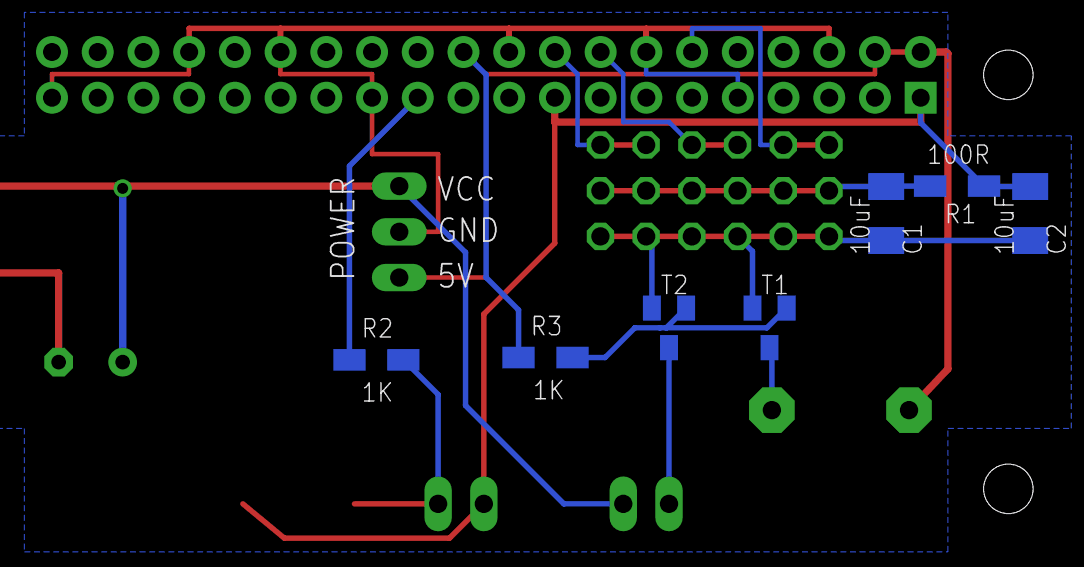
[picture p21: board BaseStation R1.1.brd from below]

Board: 2 copper layers, 19 parts (7 on the bottom side), 14 nets.

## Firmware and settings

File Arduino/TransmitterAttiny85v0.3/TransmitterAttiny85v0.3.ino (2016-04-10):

/**
 * EasyRaceLapTimer - Copyright 2015-2016 by airbirds.de, a project of polyvision UG (haftungsbeschränkt)
 *
 * Author: Alexander B. Bierbrauer
 *
 * This file is part of EasyRaceLapTimer.
 *
 * Vresion: 0.3.1
 *
 * EasyRaceLapTimer is free software: you can redistribute it and/or modify it under the terms of the GNU General Public License as published by the Free Software Foundation, either version 3 of the License, or (at your option) any later version.
 * EasyRaceLapTimer is distributed in the hope that it will be useful, but WITHOUT ANY WARRANTY; without even the implied warranty of MERCHANTABILITY or FITNESS FOR A PARTICULAR PURPOSE. See the GNU General Public License for more details.
 * You should have received a copy of the GNU General Public License along with Foobar. If not, see http://www.gnu.org/licenses/.
 **/
// use 8MHZ internal clock of the Attiny
// Timer code from http://forum.arduino.cc/index.php?topic=139729.0
#include <EEPROM.h>

#define BIT_SET(a,b) ((a) |= (1<<(b)))
#define BIT_CLEAR(a,b) ((a) &= ~(1<<(b)))
#define BIT_FLIP(a,b) ((a) ^= (1<<(b)))
#define BIT_CHECK(a,b) ((a) & (1<<(b)))

// CHANGE HERE THE ID OF TRANSPONDER
// possible values are 1 to 63
#define TRANSPONDER_ID 21

// DEFINITIONS FOR TRANSPONDERS WITH PUSH BUTTON CONFIGURATION
//#define CLEAR_EEPROM
#define ENABLE_BUTTON_CONFIGURATION
#define BUTTON_PIN PB2
#define STATUS_LED_PIN PB0
#define BUTTON_INC_ID_PUSH_TIME 750
#define LED_BLINK_CONFIRM_TIME 750
#define ENABLE_PROGRAMMING_MODE_TIME 8000 // 8 seconds

// DO NOT CHANGE ANYTHING BELOW
#define NUM_BITS  9
#define ZERO 250
#define ONE  650

unsigned int buffer[NUM_BITS];
unsigned int num_one_pulses = 0;
unsigned int transponder_id = TRANSPONDER_ID;
unsigned long buttonPushTime = 0;
int buttonState = 0;
unsigned long ledBlinkStartTime = 0;

void EEPROMWriteInt(int p_address, int p_value);
unsigned int EEPROMReadInt(int p_address);

void encodeIdToBuffer() {
  num_one_pulses = 0;
  buffer[0] = ZERO;
  buffer[1] = ZERO;
  buffer[2] = get_pulse_width_for_buffer(5);
  buffer[3] = get_pulse_width_for_buffer(4);
  buffer[4] = get_pulse_width_for_buffer(3);
  buffer[5] = get_pulse_width_for_buffer(2);
  buffer[6] = get_pulse_width_for_buffer(1);
  buffer[7] = get_pulse_width_for_buffer(0);
  buffer[8] = control_bit();
}

void readConfigButtonState() {
  if (ledBlinkStartTime != 0) {
    return;
  }

  int state = digitalRead(BUTTON_PIN);
  if (state == LOW) {
    if (state != buttonState) {
      buttonState = state;
      buttonPushTime = millis();
    }
  } else {
    buttonPushTime = millis();
  }

  buttonState = state;

  if (buttonPushTime + BUTTON_INC_ID_PUSH_TIME <= millis()) {
    transponder_id += 1;
    if (transponder_id > 63) {
      transponder_id = 1;
    }
    EEPROMWriteInt(0, transponder_id);
    ir_pulse_off();
    cli();
    buttonState = HIGH; // RESET
    buttonPushTime = millis(); // RESET
    ledBlinkStartTime = millis(); // Enable confirmation LED
    digitalWrite(STATUS_LED_PIN, HIGH);
    encodeIdToBuffer();
    sei();
    
    delay(200);
    flashTransponderId();

  }
}


void updateConfirmationLed() {
  if (ledBlinkStartTime != 0 && ledBlinkStartTime + LED_BLINK_CONFIRM_TIME <= millis()) {
    digitalWrite(STATUS_LED_PIN, LOW);
    ledBlinkStartTime = 0;
  }

}

unsigned int get_pulse_width_for_buffer(int bit) {
  if (BIT_CHECK(transponder_id, bit)) {
    num_one_pulses += 1;
    return ONE;
  }

  return ZERO;
}

unsigned int control_bit() {
  if (num_one_pulses % 2 >= 1) {
    return ONE;
  } else {
    return ZERO;
  }
}

void setup()
{
  PORTB = 0;
#ifdef CLEAR_EEPROM
  for (int i = 0 ; i < EEPROM.length() ; i++) {
    EEPROM.write(i, 0);
  }
#endif

#ifdef ENABLE_BUTTON_CONFIGURATION
  transponder_id = EEPROMReadInt(0);
  if (transponder_id == 0) {
    transponder_id = 1;
    EEPROMWriteInt(0, transponder_id);
  }

  // put your setup code here, to run once:
  pinMode(STATUS_LED_PIN, OUTPUT);
  // initialize the pushbutton pin as an input:
  pinMode(BUTTON_PIN, INPUT_PULLUP);
  PORTB |= (1 << BUTTON_PIN);    // enable pull-up resistor

  flashTransponderId();

#endif


  pinMode(PB1, OUTPUT);
  //DDRB =  0b00000010;    // set PB1 (= OCR1A) to be an output

  setFrequency(38000); // 38 kHz

  encodeIdToBuffer();
}

// Set the frequency that we will get on pin OCR1A but don't turn it on
void setFrequency(uint16_t freq)
{
  uint32_t requiredDivisor = (F_CPU / 2) / (uint32_t)freq;

  uint16_t prescalerVal = 1;
  uint8_t prescalerBits = 1;
  while ((requiredDivisor + prescalerVal / 2) / prescalerVal > 256)
  {
    ++prescalerBits;
    prescalerVal <<= 1;
  }

  uint8_t top = ((requiredDivisor + (prescalerVal / 2)) / prescalerVal) - 1;
  TCCR1 = (1 << CTC1) | prescalerBits;
  GTCCR = 0;
  OCR1C = top;
}

// Turn the frequency on
void ir_pulse_on()
{
  TCNT1 = 0;
  TCCR1 |= (1 << COM1A0);
}

// Turn the frequency off and turn off the IR LED.
// We let the counter continue running, we just turn off the OCR1A pin.
void ir_pulse_off()
{
  TCCR1 &= ~(1 << COM1A0);
}

void loop() {
  for (int i = 0; i < 3; i++) {
    for (int b = 0; b < NUM_BITS; b++) {
      switch (b) {
        case 0:
          ir_pulse_on();
          delayMicroseconds(buffer[b]);
          break;
        case 1:
          ir_pulse_off();
          delayMicroseconds(buffer[b]);
          break;
        case 2:
          ir_pulse_on();
          delayMicroseconds(buffer[b]);
          break;
        case 3:
          ir_pulse_off();
          delayMicroseconds(buffer[b]);
          break;
        case 4:
          ir_pulse_on();
          delayMicroseconds(buffer[b]);
          break;
        case 5:
          ir_pulse_off();
          delayMicroseconds(buffer[b]);
          break;
        case 6:
          ir_pulse_on();
          delayMicroseconds(buffer[b]);
          break;
        case 7:
          ir_pulse_off();
          delayMicroseconds(buffer[b]);
          break;
        case 8:
          ir_pulse_on();
          delayMicroseconds(buffer[b]);
          break;
      }
      ir_pulse_off();
    } // going through the buffer

    delay(20 + random(0, 5));
  } // 3 times

#ifdef ENABLE_BUTTON_CONFIGURATION
  readConfigButtonState();
  updateConfirmationLed();
#endif
} // end of main loop

void EEPROMWriteInt(int p_address, int p_value)
{
  byte lowByte = ((p_value >> 0) & 0xFF);
  byte highByte = ((p_value >> 8) & 0xFF);

  EEPROM.write(p_address, lowByte);
  EEPROM.write(p_address + 1, highByte);
}

unsigned int EEPROMReadInt(int p_address)
{
  byte lowByte = EEPROM.read(p_address);
  byte highByte = EEPROM.read(p_address + 1);

  return ((lowByte << 0) & 0xFF) + ((highByte << 8) & 0xFF00);
}

void flashTransponderId() {
  int fn = abs(transponder_id); //better way to find first digit of trasnponder_id
  while (fn >= 10)
    fn /= 10;

  //Display Transponder ID in two sets of LED Flashes
  for (int i = 0; i < fn; i++) { //Display MSB
    digitalWrite(STATUS_LED_PIN, HIGH);
    delay(150);
    digitalWrite(STATUS_LED_PIN, LOW);
    delay(150);
  }
  //Display a single LED Flash to seperate the bits (helps distinguish ID 1 and ID 10)
  delay(150);
  digitalWrite(STATUS_LED_PIN, HIGH);
  delay(50);
  digitalWrite(STATUS_LED_PIN, LOW);
  delay(250);

  for (int i = 0; i < transponder_id % 10; i++) { //Display LSB
    digitalWrite(STATUS_LED_PIN, HIGH);
    delay(150);
    digitalWrite(STATUS_LED_PIN, LOW);
    delay(150);
  }
}

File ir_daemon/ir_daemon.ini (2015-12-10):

[buttons]
restart_button_pin=14

[buzzer]
pin=6

[gpio_reader]
pin_0=1
pin_1=4
pin_2=5
sensorCount=3

[mode]
satellite=false

[urls]
webhost=http://localhost/

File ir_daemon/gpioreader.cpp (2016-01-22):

/**
 * EasyRaceLapTimer - Copyright 2015-2016 by airbirds.de, a project of polyvision UG (haftungsbeschränkt)
 *
 * Author: Alexander B. Bierbrauer
 *
 * This file is part of EasyRaceLapTimer.
 *
 * EasyRaceLapTimer is free software: you can redistribute it and/or modify it under the terms of the GNU General Public License as published by the Free Software Foundation, either version 3 of the License, or (at your option) any later version.
 * EasyRaceLapTimer is distributed in the hope that it will be useful, but WITHOUT ANY WARRANTY; without even the implied warranty of MERCHANTABILITY or FITNESS FOR A PARTICULAR PURPOSE. See the GNU General Public License for more details.
 * You should have received a copy of the GNU General Public License along with Foobar. If not, see http://www.gnu.org/licenses/.
 **/
#include "gpioreader.h"
#include <wiring_pi.h>
#include "buzzer.h"
#include "configuration.h"
#include <stdio.h>
#include "hoststation.h"

//#define	IR_LED_1	1
//#define	IR_LED_2	4
//#define	IR_LED_3	5

#define PULSE_ONE	500
#define PULSE_MIN 100
#define PULSE_MAX 1000

#define DATA_BIT_LENGTH 9

#define BUZZER_ACTIVE_TIME_IN_MS 100

GPIOReader::GPIOReader()
{
    this->m_bDebugMode = false;
    m_sensorCount = Configuration::instance()->sensorCount();
    for(int i = 0; i < m_sensorCount; i++) {

    }
}

bool GPIOReader::init()
{
    for(int i = 0; i < m_sensorCount; i++) {
        m_sensorPins.append(Configuration::instance()->sensorPin(i));
        if(this->m_sensorPins[i] < 0) {
            LOG_ERROR(LOG_FACILTIY_COMMON, "GPIOReader:: invalid sensor pin configuration at gpio_reader/pin_%d", i);
            return false;
        }
    }

    for(int i = 0; i < m_sensorCount; i++)
        LOG_INFO(LOG_FACILTIY_COMMON, "GPIOReader:: sensor pin %d: %i",this->m_sensorPins[i], i+1);

    for(int i = 0; i < m_sensorCount; i++)
        pinMode(this->m_sensorPins[i],INPUT);

    for(int sensor_i = 0; sensor_i < m_sensorCount; sensor_i++){
        m_sensorState.append(sensor_i);
        m_sensorPulse.append(sensor_i);

        this->m_sensorState[sensor_i] = 0;
        this->m_sensorPulse[sensor_i] = 0;

        m_sensorData.append(QList<int>());
    }

    return true;
}

void GPIOReader::reset(){
    for(int sensor_i = 0; sensor_i < m_sensorCount; sensor_i++){
        this->m_sensorState[sensor_i] = 0;
        this->m_sensorPulse[sensor_i] = 0;
        this->m_sensorData[sensor_i].clear();
    }
    m_sensoredTimes.clear();
    LOG_INFOS(LOG_FACILTIY_COMMON, "GPIOReader::resetted");
}

void GPIOReader::setDebug(bool v){
    this->m_bDebugMode = v;
    if(this->m_bDebugMode){
        LOG_INFOS(LOG_FACILTIY_COMMON, "GPIOReader enabled debugging mode");
    }
}

unsigned int GPIOReader::num_ones_in_buffer(QList<int>& list){
    unsigned int t= 0;
    for(int i=0; i < list.length(); i++){ // -1 because we don't count the last bit.. it's the checksum bit!
        if(list[i] == 1){
            t += 1;
        }
    }
    return t;
}


void GPIOReader::print_binary_list(QList<int>& list){
    for(int i=0; i < list.length(); i++){
        if(list[i] == 1){
            LOG_DBGS(LOG_FACILTIY_COMMON, "1");
        }else{
            LOG_DBGS(LOG_FACILTIY_COMMON, "0");
        }
    }
}

void GPIOReader::push_to_service(int sensor_i,QList<int>& list,int control_bit){
    unsigned int val_to_push = 0;
    if(this->m_bDebugMode){
    	print_binary_list(list);
    }

    list.removeFirst();
    list.removeFirst();
    list.removeLast();

    for(int i=0; i < list.length(); i++){
        if(list[i] == 1){
            BIT_SET(val_to_push,list.length() - i -1);
        }else{
            BIT_CLEAR(val_to_push,list.length() -i - 1 );
        }
    }

    int own_control_bit = (int)num_ones_in_buffer(list) % 2;

    if(control_bit == own_control_bit){
        QString token = QString("%1").arg(val_to_push);

        HostStation::instance()->setLastScannedToken(token);
        
        if(m_sensoredTimes[token] == 0){
        	m_sensoredTimes[token] = millis();
        }else if(m_sensoredTimes[token] + 1000 < millis()){
        	unsigned int delta_time = millis() - m_sensoredTimes[token];
        	Buzzer::instance()->activate(BUZZER_ACTIVE_TIME_IN_MS);
        	emit newLapTimeEvent(token,delta_time);
        	m_sensoredTimes[token] = millis();
        }

    }else{
        LOG_WARN(LOG_FACILTIY_COMMON, "sensor: %i control bit wrong: %i own_control_bit: %i, token: %u",sensor_i,control_bit,own_control_bit,val_to_push);
    }
}
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

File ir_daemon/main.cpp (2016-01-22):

/**
 * EasyRaceLapTimer - Copyright 2015-2016 by airbirds.de, a project of polyvision UG (haftungsbeschränkt)
 *
 * Author: Alexander B. Bierbrauer
 *
 * This file is part of EasyRaceLapTimer.
 *
 * EasyRaceLapTimer is free software: you can redistribute it and/or modify it under the terms of the GNU General Public License as published by the Free Software Foundation, either version 3 of the License, or (at your option) any later version.
 * EasyRaceLapTimer is distributed in the hope that it will be useful, but WITHOUT ANY WARRANTY; without even the implied warranty of MERCHANTABILITY or FITNESS FOR A PARTICULAR PURPOSE. See the GNU General Public License for more details.
 * You should have received a copy of the GNU General Public License along with Foobar. If not, see http://www.gnu.org/licenses/.
 **/

#include <QtCore/QCoreApplication>
#include <stdio.h>
#include <QProcess>
#include <QTextStream>
#include <QtConcurrent>
#include <curl/curl.h>
#include "restart_button_input.h"
#include "buzzer.h"
#include "gpioreader.h"
#include "networkserver.h"
#include "hoststation.h"
#include "serialconnection.h"
#include "configuration.h"
#include "infoserver.h"
#include "logger.h"

#define VERSION "0.4"

#include <wiring_pi.h>

int main(int argc, char *argv[])
{
    QCoreApplication a(argc, argv);
    QCoreApplication::setOrganizationName("polyvision UG");
    QCoreApplication::setOrganizationDomain("polyvision.org");
    QCoreApplication::setApplicationName("ir_daemon");

    curl_global_init(CURL_GLOBAL_ALL);

    Logger::instance()->init();

    LOG_INFO(LOG_FACILTIY_COMMON, "starting ir_daemon v%s\n", VERSION);

	if(a.arguments().count() > 1){
        if(a.arguments().at(1).compare("--debug") == 0){
            Configuration::instance()->setDebug(true);
            GPIOReader::instance()->setDebug(true);
            LOG_DBGS(LOG_FACILTIY_COMMON, "enabled debug mode");
		}

        if(a.arguments().at(1).compare("--list_serial_ports") == 0){
            SerialConnection::listAvailablePorts();
            return 0;
        }

        if(a.arguments().at(1).compare("--set_com_port_index") == 0){
            Configuration::instance()->setComPortIndex(a.arguments().at(2).toInt());
            return 0;
        }

        if(a.arguments().at(1).compare("--set_web_host") == 0){
            Configuration::instance()->setWebHost(a.arguments().at(2));
            return 0;
        }

        if(a.arguments().at(1).compare("--set_buzzer_pin") == 0){
            Configuration::instance()->setBuzzerPin(a.arguments().at(2).toInt());
            return 0;
        }

        if(a.arguments().at(1).compare("--enable_satellite_mode") == 0){
            Configuration::instance()->setSatelliteMode(true);
            return 0;
        }

        if(a.arguments().at(1).compare("--disable_satellite_mode") == 0){
            Configuration::instance()->setSatelliteMode(false);
            return 0;
        }

        if(a.arguments().at(1).compare("--use_standard_gpio_sensor_pins") == 0){
            Configuration::instance()->setSensorCount(3);
            Configuration::instance()->setSensorPin(0,1);
            Configuration::instance()->setSensorPin(1,4);
            Configuration::instance()->setSensorPin(2,5);
            Configuration::instance()->setBuzzerPin(6);
            Configuration::instance()->setRestartButtonPin(14);
            return 0;
        }

        if(a.arguments().at(1).compare("--use_dot3k_hat_pin_setup") == 0){
            Configuration::instance()->setSensorCount(3);
            Configuration::instance()->setSensorPin(0,21);
            Configuration::instance()->setSensorPin(1,22);
            Configuration::instance()->setSensorPin(2,23);
            Configuration::instance()->setBuzzerPin(24);
            Configuration::instance()->setRestartButtonPin(25);
            return 0;
        }
	}

    //initialization
    wiringPiSetup ();
    HostStation::instance()->setup();
    Buzzer::instance()->setPin(Configuration::instance()->buzzerPin());
    RestartButtonInput::instance()->setPin(Configuration::instance()->restartButtonPin());
    InfoServer::instance();

    SerialConnection::instance()->setup();

    if(!GPIOReader::instance()->init()) {
        return -1;
    }

	while(1){
        GPIOReader::instance()->update();
		Buzzer::instance()->update();
        RestartButtonInput::instance()->update();
        a.processEvents();
	}

    curl_global_cleanup();
    return a.exec();
}

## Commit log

2015-11-08 3 sensor support added buzzer support
    [main.cpp]
2015-11-08 added gpio wiring for raspberry2
2015-11-13 websockets r now configurable via env variable RAILS_CABLE_IP
2015-11-15 lots of GUI improvements and new stats preparing first stable release
    [sensor_case.scad, sensor_case.stl]
2015-11-16 preparing first stable release
    [sensor_case.scad, sensor_case.stl]
2015-11-17 changed ir_daemon to 9 bit mode POST requests in seperate threads
2015-11-17 added Arduino files for the new 9bit transponder docs updated etc
2015-11-23 added button support on PIN 14 to start a new race started to clean up ir_daemon code
2015-11-25 bug fixes for the rails app improved ir_daemon
    [configuration.h]
2015-11-27 upcomming v0.3 added sensor case for different direction started to write update instructions, not complete yet
    [sensor_case.scad, sensor_case_left.stl]
2015-12-02 added lcd support (Displayotron 3000 HAT) support by adding an info server added more config switches to the ir_daemon
    [configuration.h]
2015-12-07 fixed a bug with double using transponder tokens
    [gpioreader.cpp, hoststation.cpp, main.cpp]
2015-12-07 satellite mode for the ir_daemon
    [configuration.h]
2015-12-08 various bug fixes
    [configuration.h]
2015-12-10 added version info the gui fixex image bug in pdf export
    [TransmitterAttiny85v0.2.ino]
2015-12-10 - refactoring - added logging class for syslog and console logging (file is todo) - possibility to add more ir sensors via config file
    [configuration.h]
2015-12-10 updated testing code for Arduino Nano
2015-12-19 removed action cable code
2015-12-22 fix for button visibility
2015-12-22 button visibility
2015-12-23 fixed typos and updated docs
    [configuration.h]
2016-01-06 updated documentation small fixes added pdb fritzing file
    [easy_race_lap_timer_raspberry_2_sensor_shield_rev1.fzz]
2016-01-12 race director shows now current race information
2016-01-17 first working version of race director in the web gui improved some things and fixed a couple of bugs in ir_daemon
    [hoststation.cpp]
2016-02-14 Kicad transmitter circuit and PCB
    [transmitter.kicad_pcb, transmitter.sch]
2016-02-16 Kicad PCB layout
    [transmitter.kicad_pcb, transmitter.sch]
2016-02-16 Revert "Kicad PCB layout"
    This reverts commit 9afb40ae9a6d2ea0d6b4d8b9758429dc2c52fee4.
    [transmitter.kicad_pcb, transmitter.sch]
2016-02-16 Revert "Kicad transmitter circuit and PCB"
    This reverts commit 51ba06ca087ca7753eddb7d80b7d77b9e4b8eb6c.
    [transmitter.kicad_pcb, transmitter.sch]
2016-02-17 Add wiringpi to the list of required packages before building ir_daemon
2016-03-06 updates some docs, added transponder 0.3.1 schematic
2016-03-15 IR sensor mount
    Alternative 3D printed IR receiver mount for TSOP31238. These are designed to mounted to the back side of agate with 1/4" or 5-6mm wide zip ties. The TSOP is held in the mount with double sided foam 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
    [ERLT Sensor Left - TSOP31238.skp, ERLT Sensor Left - TSOP31238.stl, ERLT Sensor Right - TSOP31238.skp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]
2016-03-15 PCB Files for SMD Transponder and Pi Hat Base Station
    [BaseStation R1.1.brd, BaseStation R1.1.sch, SMD R1.4.brd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]
2016-03-31 Reroute LED and transistor. Remove backup files from git.
    [transmitter.kicad_pcb, transmitter.sch]
2016-04-01 Adding screenshot of Pi Hat Base Station schematic
2016-04-01 Adding screenshot of SMD R1.4 schematic
2016-04-06 Replace 3 blink startup with transponder id
    replace the 3 blink startup with two sets of blinks (with a blink in between) to display the MSB and LSB of the transponder ID. for example 21 will be displayed as 2 quick blinks, a separating blink, and another blink.
    [TransmitterAttiny85v0.3.ino]
2016-04-09 fix bug with trasponder id flash on setup hanging
    [TransmitterAttiny85v0.3.ino]
2016-04-12 Editing component list
    Added TSUS5202 as additional example of IR LED
    Changed 56 Ohm resistor to 33 Ohm for increased LED output.
    Added Edimax EW-7811Un as example USB WiFi adapter
2016-04-15 Fixed broken link for Transponder 0.3.1 schematic
2016-04-15 Add -bak to list of ignored files to catch a few kicad backup files
2016-05-20 Cleaning up formatting
    I screwed up the code formatting and the back-ticks were visible.
2021-02-18 Updated to rails 4.2.11.3 to run on modern systems
